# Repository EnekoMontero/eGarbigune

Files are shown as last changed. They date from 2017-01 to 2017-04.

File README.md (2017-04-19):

# eGarbigune :recycle:
 > Probably the cheapest mini 3D printer in the world. :moneybag:<br/>
 > Probablemente la mini impresora 3D más barata del mundo. :moneybag:

## Especificaciones principales
 - Mini impresora 3D hecha a partir de componentes reciclados
 - Replicable
 - Electrónica: Arduino Mega + Ramps 1.4
 - Firmware: Marlin
 - Volumen de impresión: 40x40x40 mm^3 teóricos
 - Sistema de ejes cartesianos
 - Hotend tipo J-Head con bowden
 - Base nivelable sin cama caliente
 - Materiales: PLA
 - Velocidad: 20-40mm/s

## Instrucciones de montaje
[Índice - Guía de montaje](http://haudahau.com/vadedos/?p=906)
 1. [Lista de materiales](http://haudahau.com/vadedos/?p=952)
 2. [Preparando los lectores de cd/dvd](http://haudahau.com/vadedos/?p=982)
 3. [Impresión de piezas](http://haudahau.com/vadedos/?p=1000)
 4. [Montaje de la estructura y del extrusor](http://haudahau.com/vadedos/?p=1026)
 5. [Electrónica y cableado](http://haudahau.com/vadedos/?p=1057)
 6. [Calibración y primera pieza](http://haudahau.com/vadedos/?p=1081)
 7. [Ponerla "coqueta", últimos detalles](http://haudahau.com/vadedos/?p=1115)
 8. Anexo
	 1. [Comprobar que los motores se mueven](http://haudahau.com/vadedos/?p=843)
	 2. [Añadir una impresora 3D en el Cura](http://haudahau.com/vadedos/?p=1095)
 9. Sácale fotos y házmelas llegar vía [twitter](https://twitter.com/enekomontero) u otros medios para añadirlas en GitHub :grin:

## Fotos
Fotos | :camera:
-------- | ---
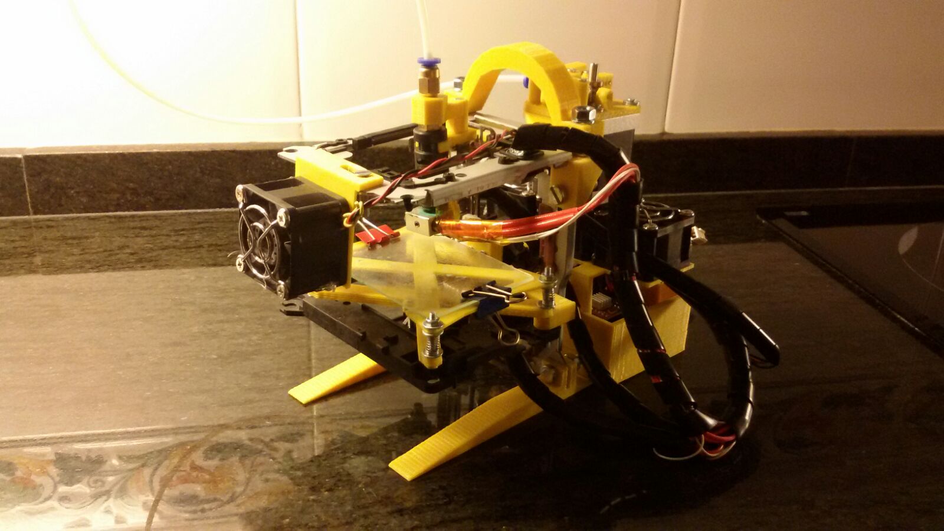
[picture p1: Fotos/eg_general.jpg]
general
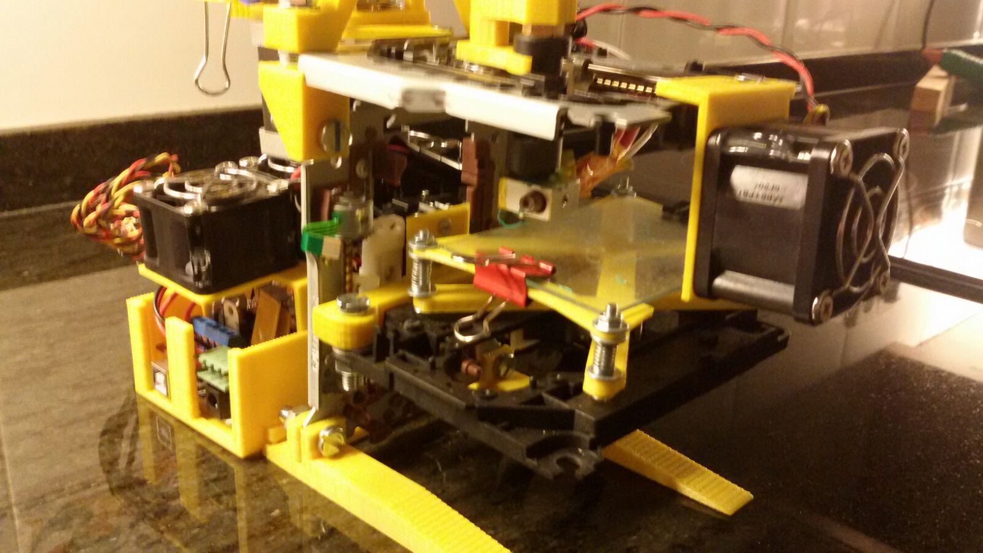
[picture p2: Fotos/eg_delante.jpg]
delante
  |  
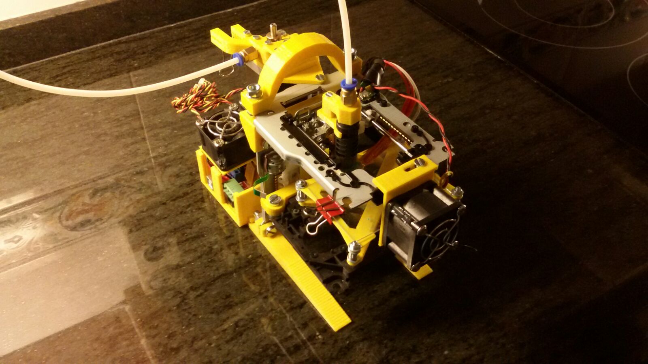
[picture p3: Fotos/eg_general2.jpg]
general2
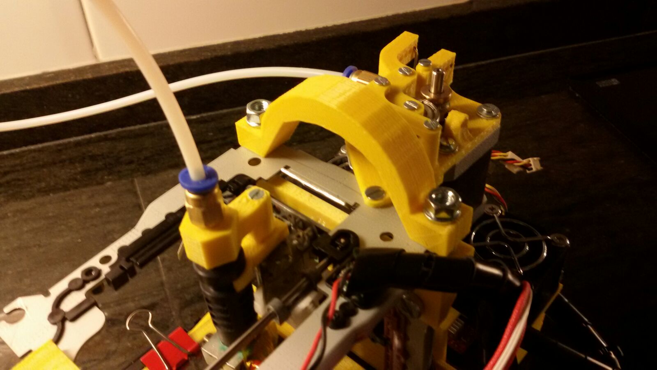
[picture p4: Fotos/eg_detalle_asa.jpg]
detalle asa
 |  
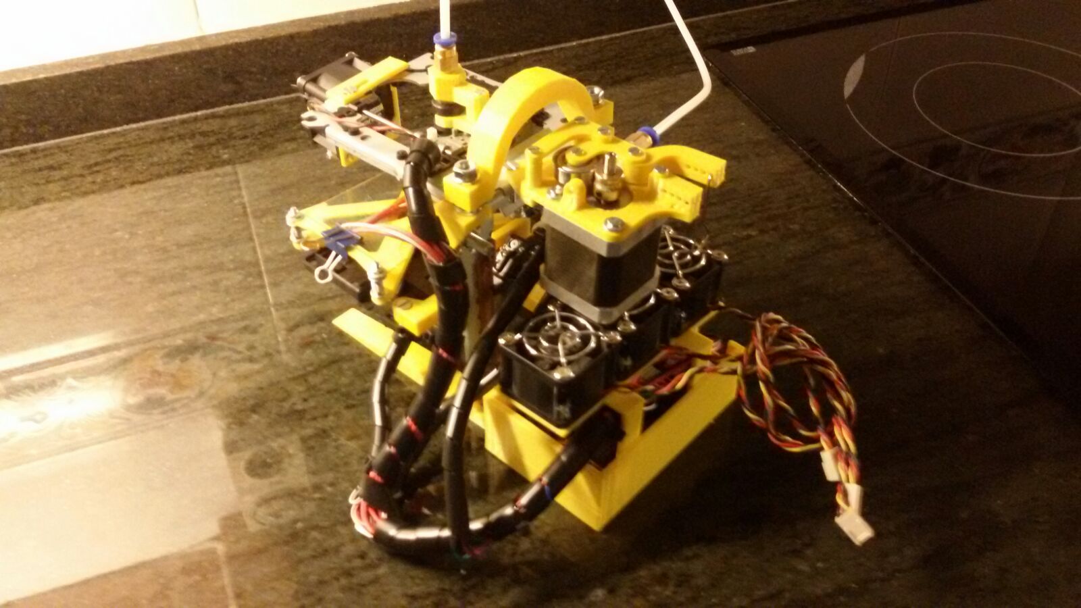
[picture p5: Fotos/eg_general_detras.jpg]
general detras
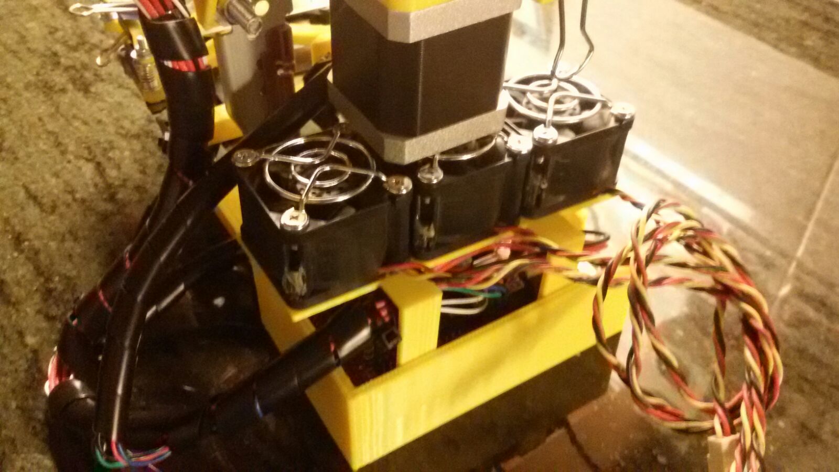
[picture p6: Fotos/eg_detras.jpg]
detrás
  |  
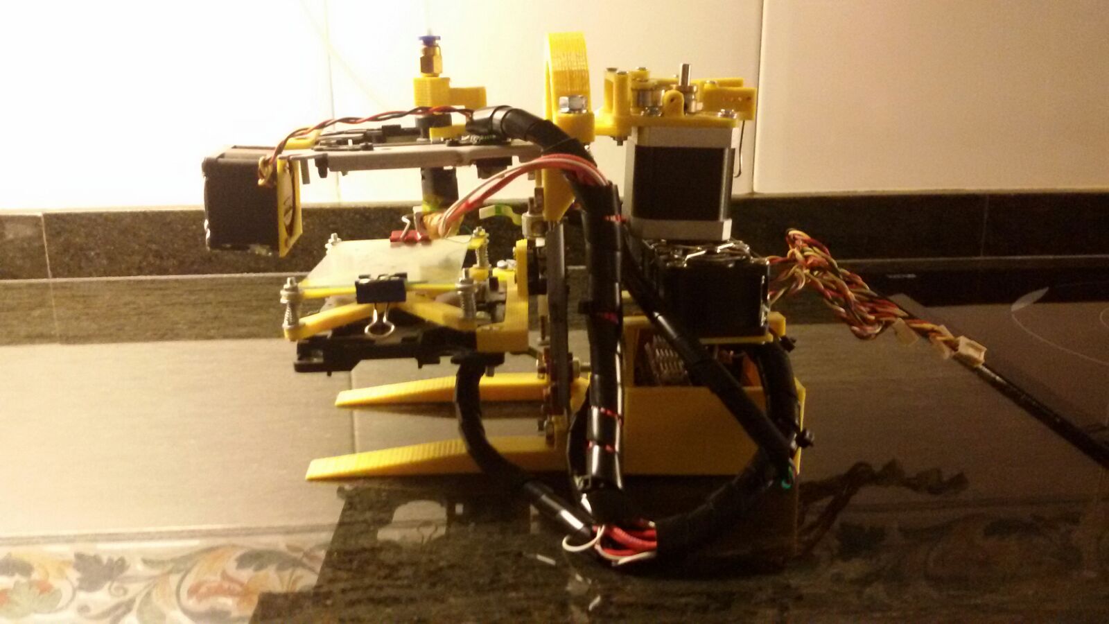
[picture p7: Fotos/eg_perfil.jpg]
perfil
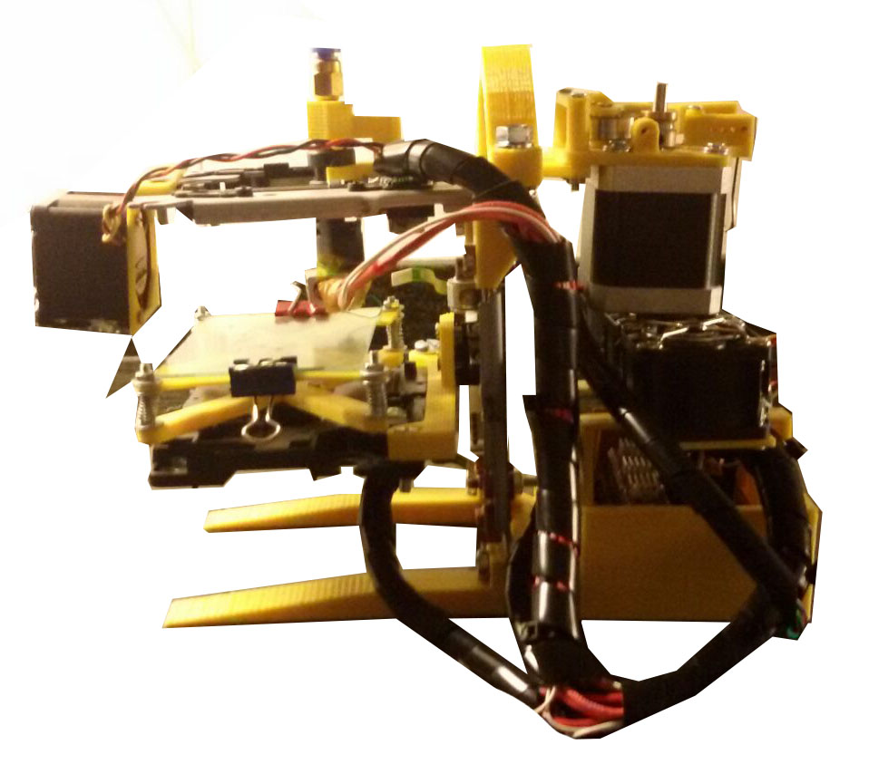
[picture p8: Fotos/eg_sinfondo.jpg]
perfil sin fondo
 |  

## eGarbigunes por el mundo :earth_africa:
Samuel Gil | :round_pushpin: Santiago de Compostela
-------- | ---
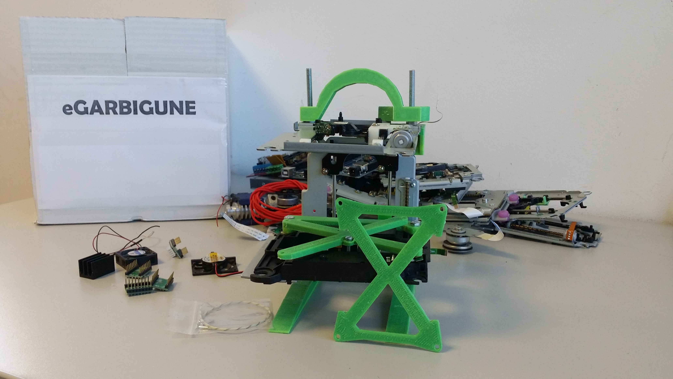
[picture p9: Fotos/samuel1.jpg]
samuel1
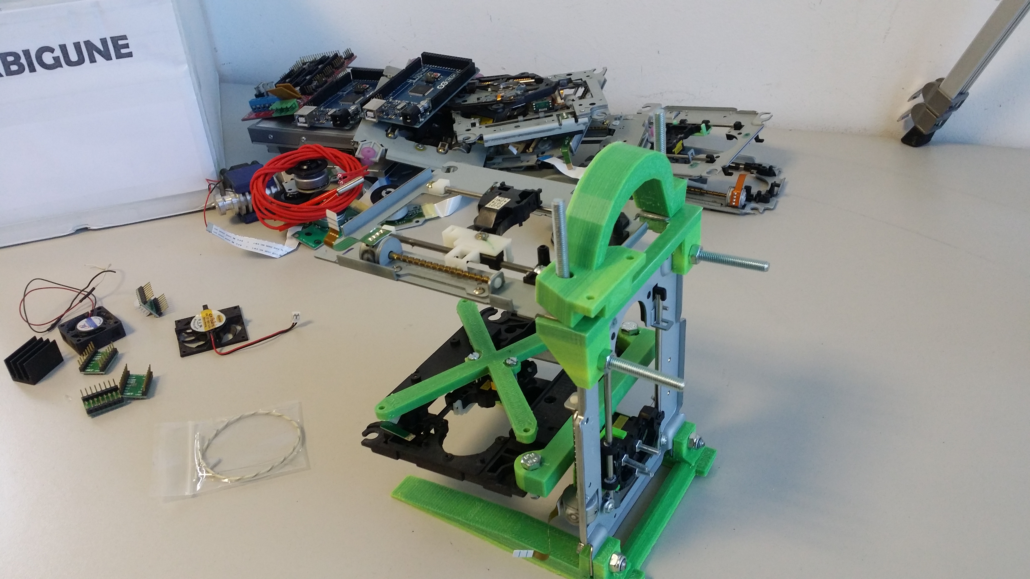
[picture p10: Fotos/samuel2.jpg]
samuel2
  | 

[bolsoncerrado](http://print3dforum.com/) | :round_pushpin: Barcelona
-------- | ---
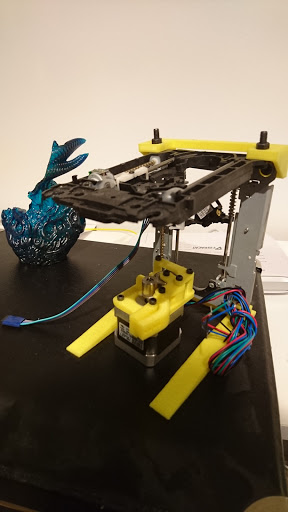
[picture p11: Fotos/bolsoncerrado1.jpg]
bolsoncerrado1
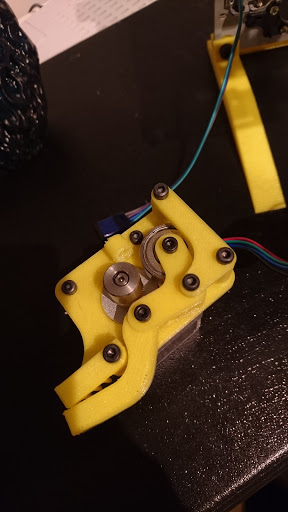
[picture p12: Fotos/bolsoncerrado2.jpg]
bolsoncerrado2
  | 
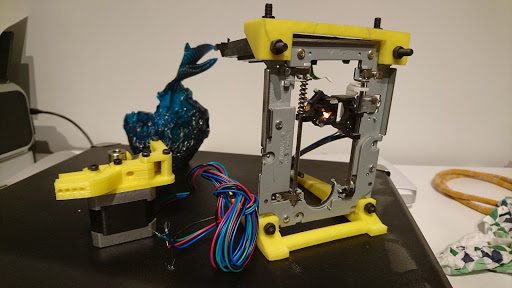
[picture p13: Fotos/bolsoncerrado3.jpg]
bolsoncerrado3
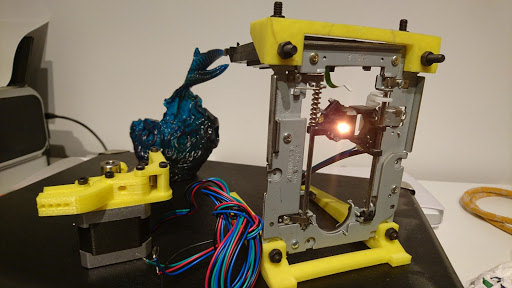
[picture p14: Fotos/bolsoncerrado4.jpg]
bolsoncerrado4
  | 

## Vídeos
 - Mini 3D Printer - First attempt [[youtube]](https://www.youtube.com/watch?v=VHxQsBB6kfk)
 - eGarbigune - Mini 3D Printer [[youtube]](https://www.youtube.com/watch?v=phJxERG1OLM&t=1s)
 
## Algunos artículos donde aparece
 - <http://haudahau.com/vadedos/?page_id=906>
 - <https://3dprint.com/94400/egarbigune-3d-printer/>
 - <http://impresiontresde.com/blog/egarbigune-una-mini-impresora-3d-reciclando-viejos-componentes-electronicos/>
 - <http://3dprintingfromscratch.com/2015/10/eneko-monteros-3d-printer-from-recycled-parts/>
 - <http://www.semageek.com/egarbigune-la-mini-imprimante-3d-fabriquee-avec-des-pieces-recyclees/>
 - <http://maker8.com/article-4497-1.html>
 - <http://www.3dhoo.com/news/guowai/21030.html>
 - <http://dimglobal.ning.com/group/roboticadonostia16/forum/topics/egarbigune-mini-impresora-3d-reciclada>

## Autor
 - Eneko Montero
 
## Licencia
<p style="text-align: justify;"><br/>
<a href="http://haudahau.com/vadedos/?page_id=906" target="_blank">eGarbigune</a> por <a href="https://es.linkedin.com/in/enekomontero" target="_blank" rel="cc:attributionURL">Eneko Montero</a> se distribuye bajo una <a href="http://creativecommons.org/licenses/by-sa/4.0/" target="_blank" rel="license">Licencia Creative Commons Atribución-CompartirIgual 4.0 Internacional</a>.</p>

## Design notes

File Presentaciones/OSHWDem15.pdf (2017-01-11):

# eGarbigune

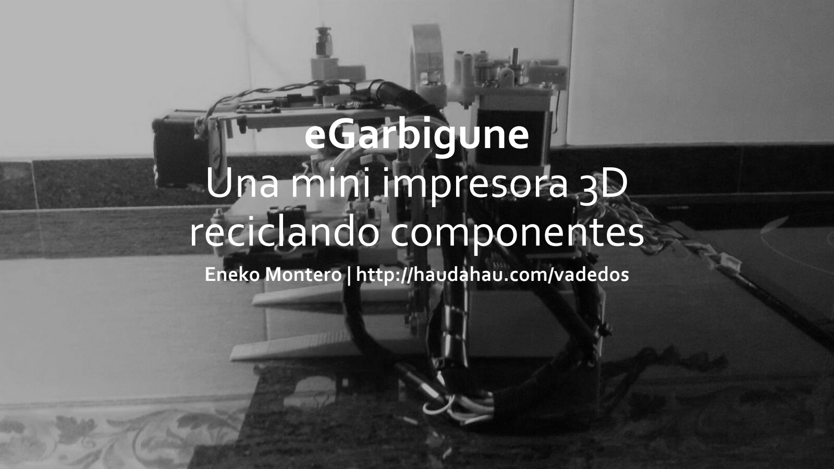
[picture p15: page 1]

# Una mini impresora 3D reciclando componentes

### Eneko Montero | http://haudahau.com/vadedos

# Especificaciones principales

- Mini impresora 3D hecha a partir de componentes reciclados
- Replicable
- Electrónica: Arduino Mega + Ramps 1.4
- Firmware: Marlin
- Volumen de impresión: 40x40x40 mm^3 teóricos
- Sistema de ejes cartesianos
- Hotend tipo J-Head con bowden
- Base nivelable sin cama caliente
- Materiales: PLA
- Velocidad: 20-40mm/s

# Proceso de montaje

### Lo que iba a ser y no fue

Se iba a basar en el proyecto eWaste,

### pero con una estructura impresa en 3D

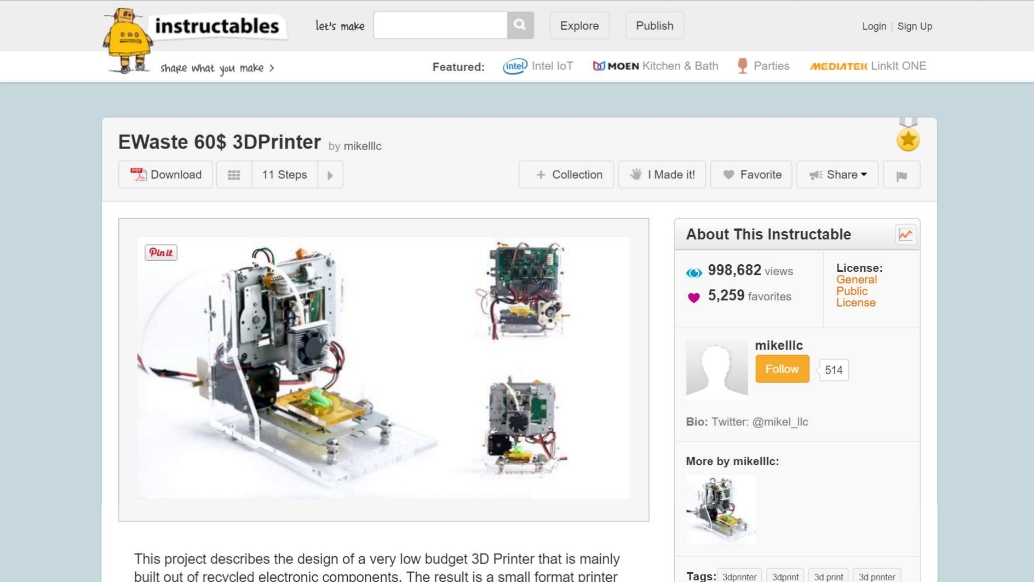
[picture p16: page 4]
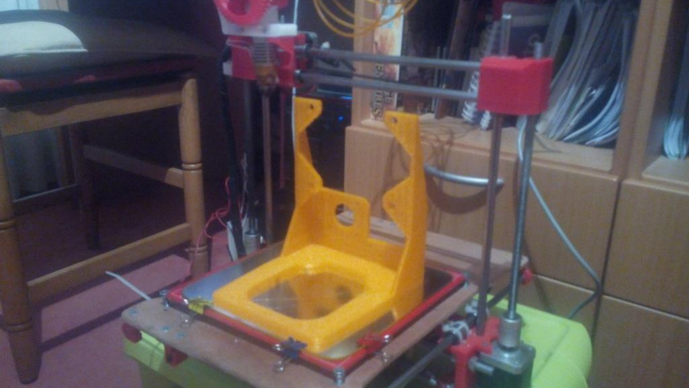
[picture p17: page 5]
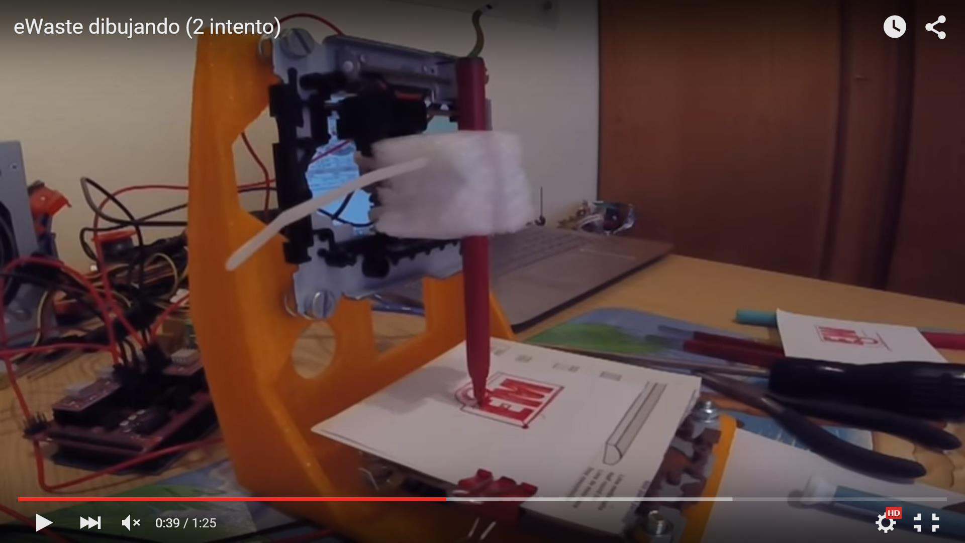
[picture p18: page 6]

# Encaminando el proyecto

Lo que finalmente fue, eGarbigune, misma idea, distinta ejecución

1. Reciclar lectores de cd/dvd
2. Imprimir las piezas necesarias para la estructura en 3D
3. Sistema de ejes distinto a eWaste

# Sistema de movimiento

Ejes cartesianos

- Eje X | Movimiento de la base de impresión con un lector de plástico.
- Eje Y | Movimiento del hotend con un lector metálico en la parte superior.
- Eje Z | Movimiento de la base con un único lector metálico en vertical. El lector del eje x va encajado a este. Comienza en la parte superior y va bajando según avanza la impresión.
- Homing | No lleva endstops, indicamos la posición (0,0,0) antes de comenzar la impresión.

## Reciclaje de lectores de

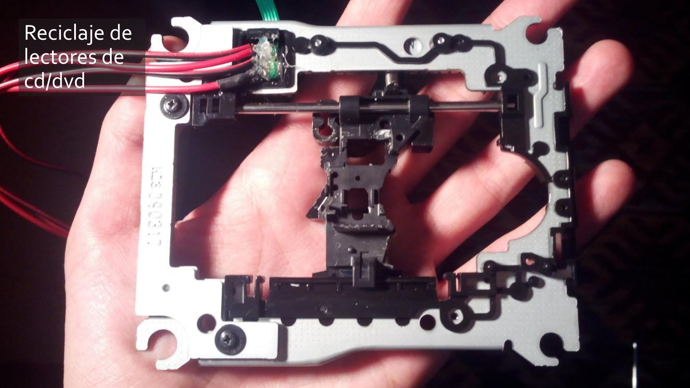
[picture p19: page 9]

## cd/dvd

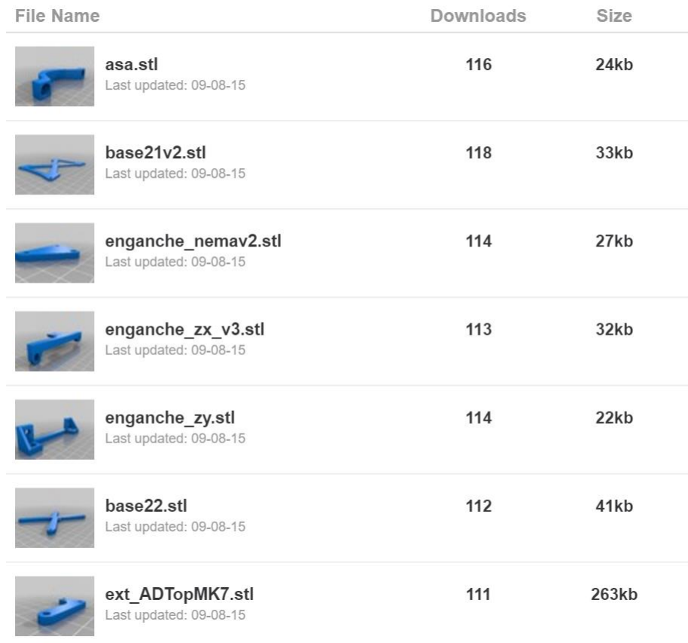
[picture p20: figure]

# Impresión de piezas

- Diseñadas usando SketchUp
- Se imprimen sin soportes*
- Se pueden descargar en Thingiverse (http://www.thingiverse.com/thing:1003982/#files)

*excepto una que no es necesaria en todos los casos

# Extrusor con bowden

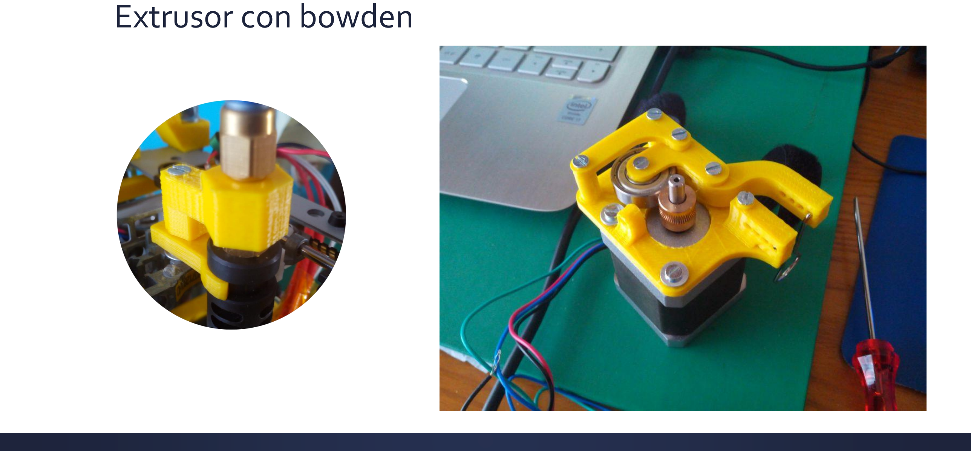
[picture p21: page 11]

# Primera pieza

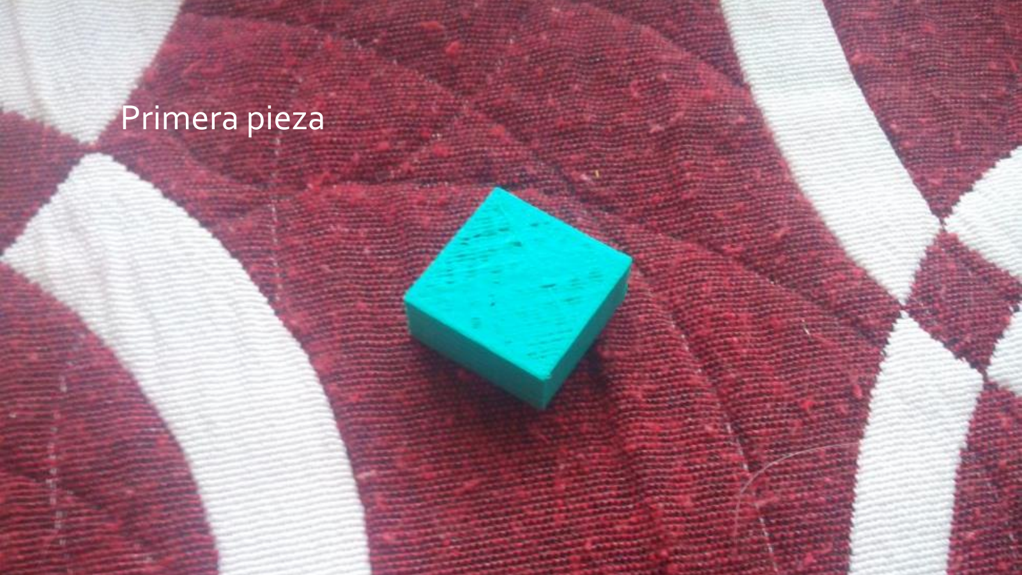
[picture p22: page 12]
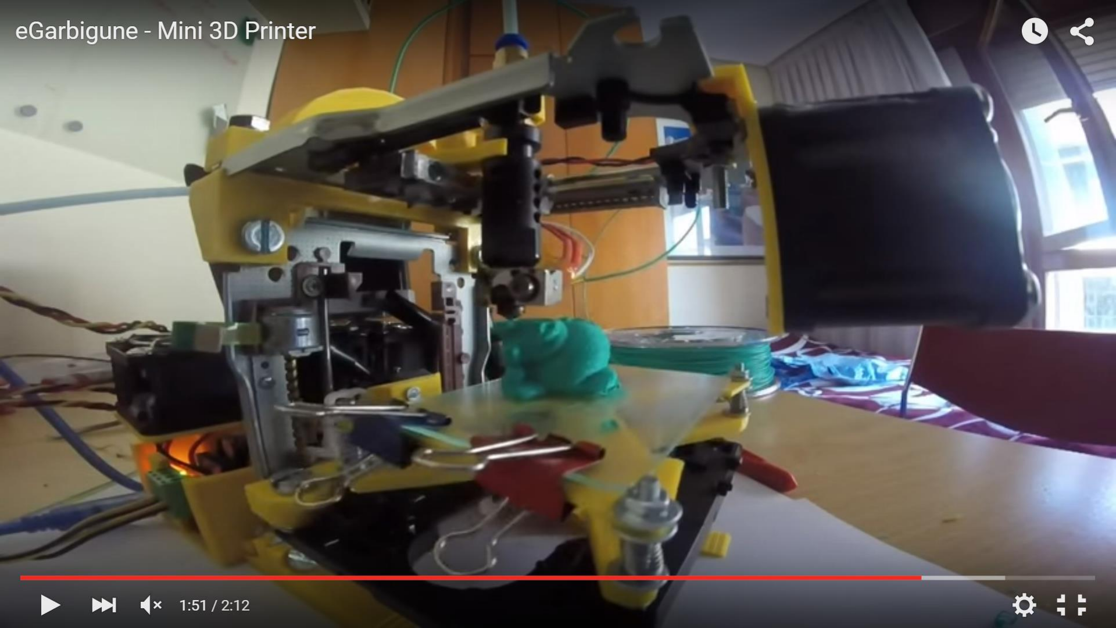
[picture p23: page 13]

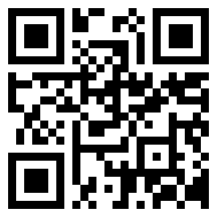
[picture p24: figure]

# FIN

### Eneko Montero

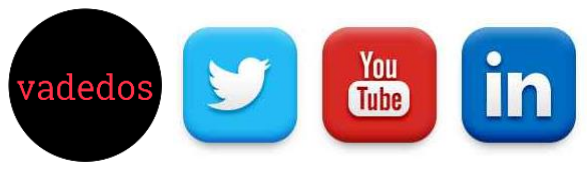
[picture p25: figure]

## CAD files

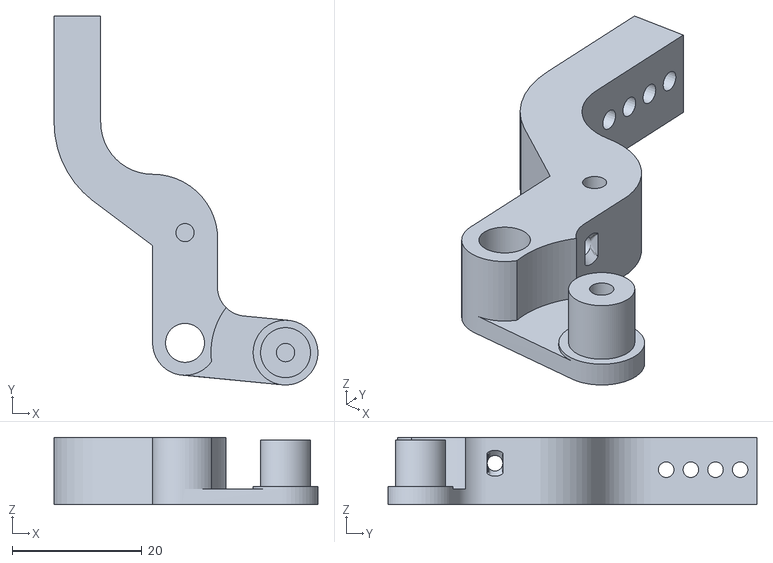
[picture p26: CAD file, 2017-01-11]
STL/ext_ADLowerArmMK7_R2.stl
40.7 x 56.9 x 10.4

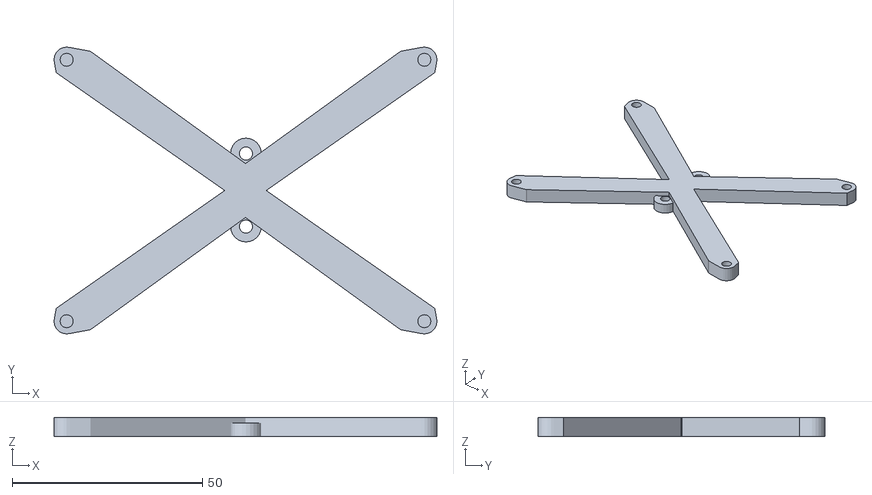
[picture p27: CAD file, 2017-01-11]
STL/base22.stl
100.6 x 75.3 x 5.00

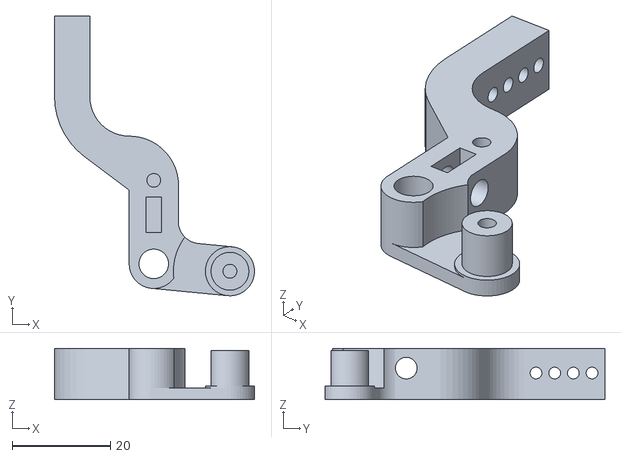
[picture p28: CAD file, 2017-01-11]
STL/ext_ADLowerArmAltMK7_R2.stl
40.7 x 56.9 x 10.4

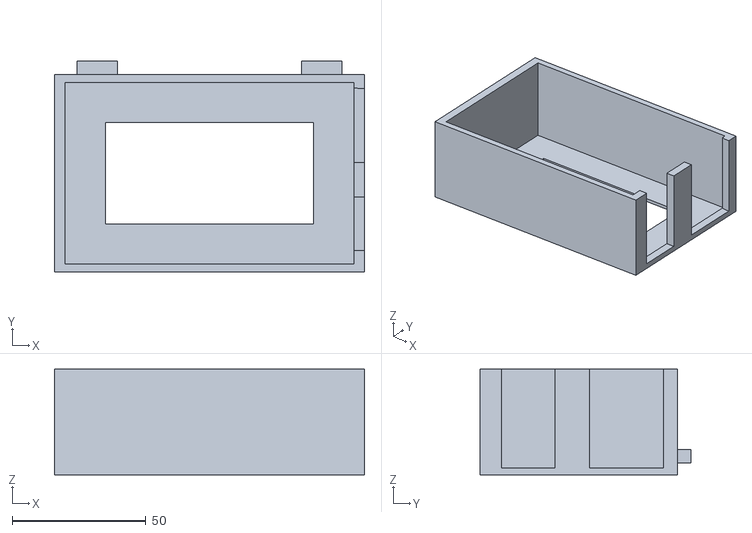
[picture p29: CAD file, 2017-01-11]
STL/rampscase.stl
116.0 x 79.0 x 39.5

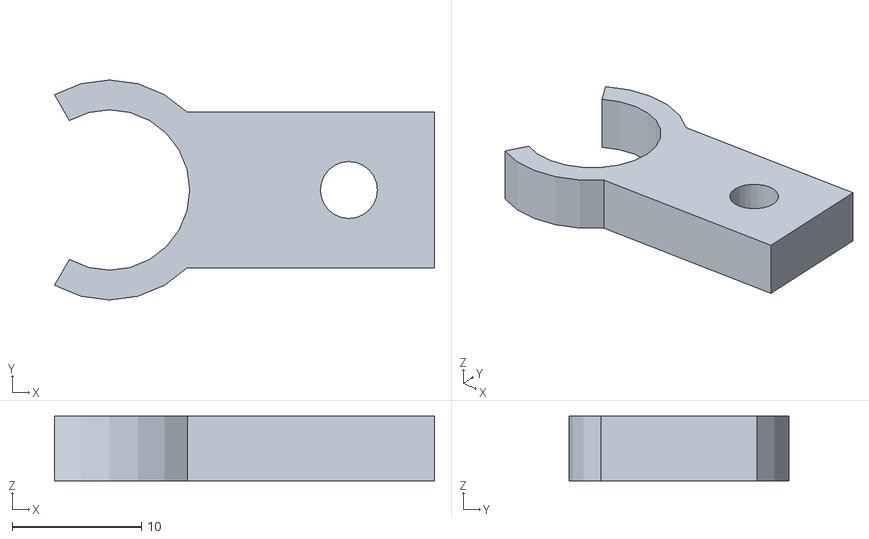
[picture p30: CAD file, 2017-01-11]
STL/soporte hotendv3.stl
29.4 x 17.0 x 5.00

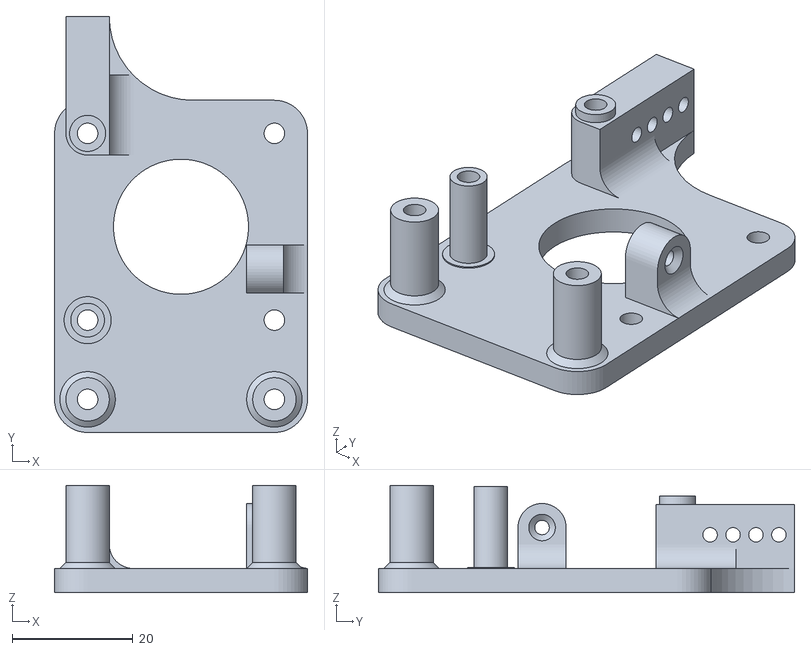
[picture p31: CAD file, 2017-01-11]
STL/ext_ADBaseMK7_R2.stl
42.0 x 69.0 x 17.8

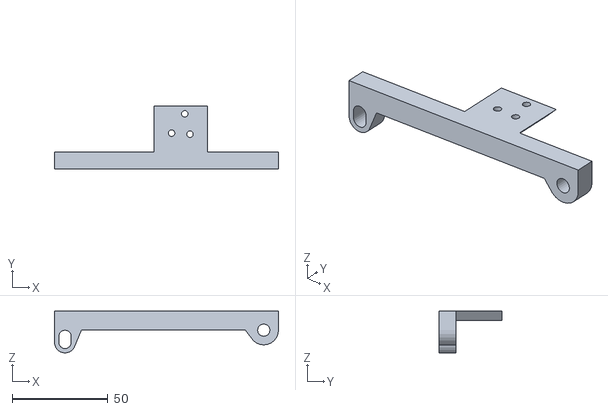
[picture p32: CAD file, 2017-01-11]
STL/enganche_zx_v3.stl
117.0 x 33.0 x 21.9

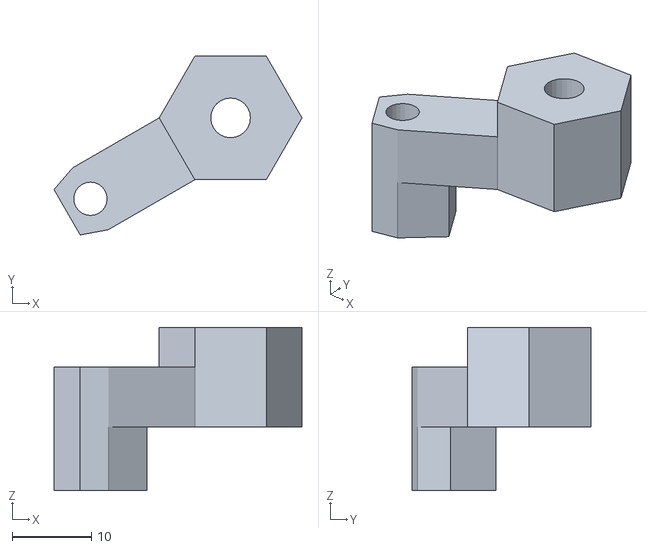
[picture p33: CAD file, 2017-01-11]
STL/racor.stl
31.3 x 22.5 x 20.6

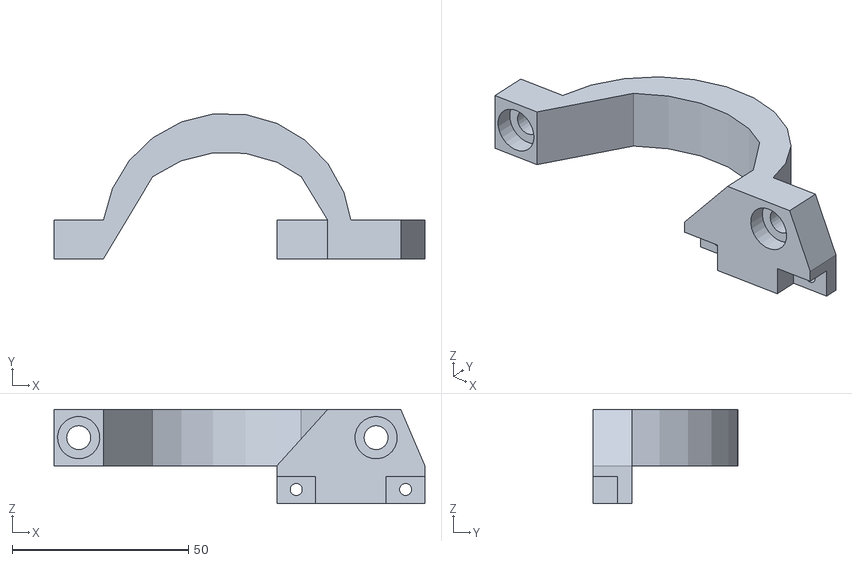
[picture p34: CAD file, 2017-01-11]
STL/asav2.stl
105.2 x 41.1 x 26.7

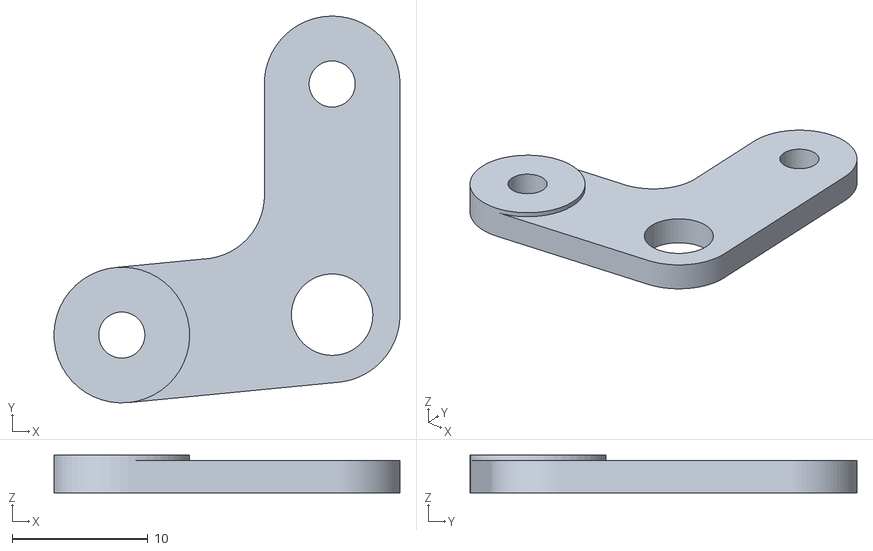
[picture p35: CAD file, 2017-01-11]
STL/ext_ADUpperArmMK7.stl
25.5 x 28.5 x 2.80

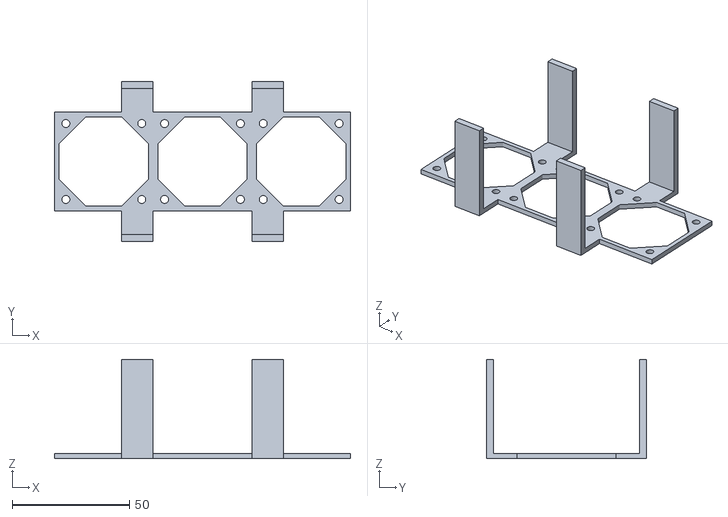
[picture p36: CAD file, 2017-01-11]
STL/vent_electro.stl
126.0 x 68.0 x 42.2

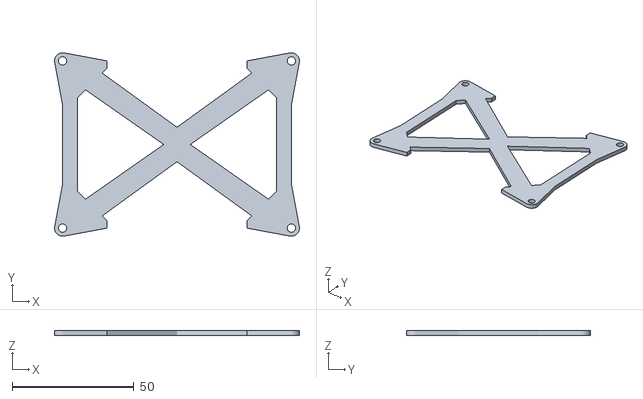
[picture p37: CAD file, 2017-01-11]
STL/base21v2.stl
100.6 x 75.3 x 2.00

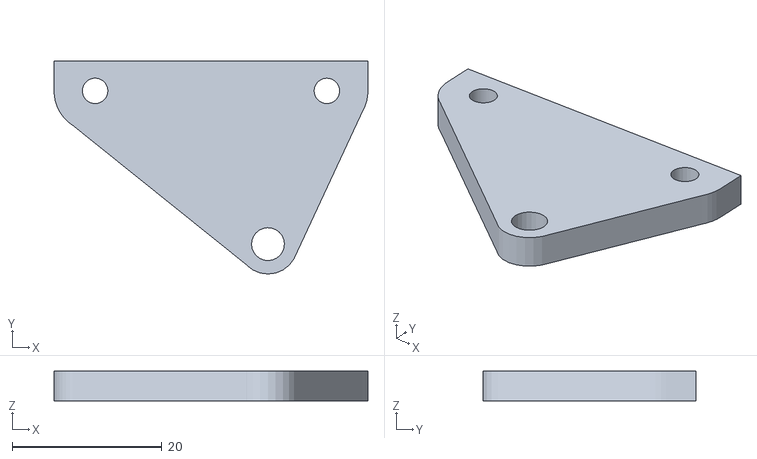
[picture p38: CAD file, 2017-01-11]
STL/enganche_nemav2.stl
42.0 x 28.5 x 4.00

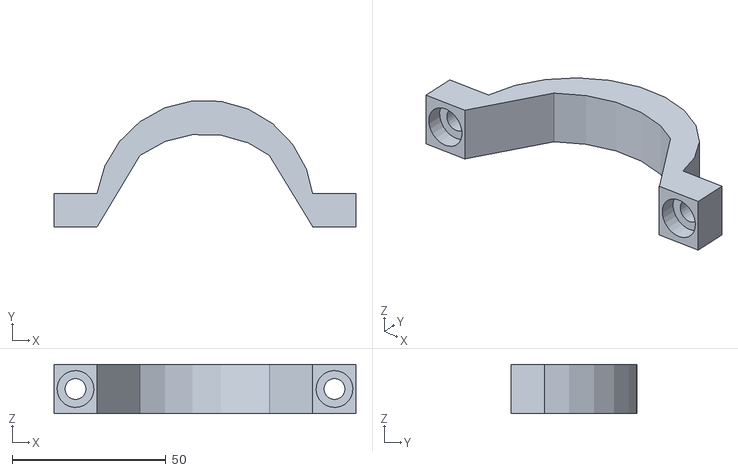
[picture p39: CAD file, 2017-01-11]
STL/asa.stl
98.3 x 41.1 x 16.0

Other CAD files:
STL/ext_ADTopMK7.stl
STL/vent_hotend.stl
STL/enganche_zy.stl
STL/patav2.stl
SKP/asa.skp
SKP/asav2.skp
SKP/base21v2.skp
SKP/enganche zx v3.skp
SKP/enganche zy.skp
SKP/enganche_nemav2.skp
SKP/patav2.skp
SKP/racor.skp
SKP/rampscase.skp
SKP/soporte hotend.skp
SKP/ventiladores.skp

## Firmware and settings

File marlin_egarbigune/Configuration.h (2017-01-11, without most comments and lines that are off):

#define CONFIGURATION_H
#define STRING_VERSION_CONFIG_H __DATE__ " " __TIME__ // build date and time
#define STRING_CONFIG_H_AUTHOR "Eneko Montero" //Who made the changes.
#define SERIAL_PORT 0
#define BAUDRATE 250000
#define MOTHERBOARD 33
#define POWER_SUPPLY 1
#define TEMP_SENSOR_0 5
#define TEMP_SENSOR_1 5
#define TEMP_SENSOR_2 5
#define TEMP_SENSOR_BED 5
#define TEMP_RESIDENCY_TIME 10	// (seconds)
#define TEMP_HYSTERESIS 3       // (degC) range of +/- temperatures considered "close" to the target one
#define TEMP_WINDOW     1       // (degC) Window around target to start the recidency timer x degC early.
#define HEATER_0_MINTEMP 0
#define HEATER_1_MINTEMP 0
#define HEATER_2_MINTEMP 0
#define BED_MINTEMP 0
#define HEATER_0_MAXTEMP 250
#define HEATER_1_MAXTEMP 250
#define HEATER_2_MAXTEMP 250
#define BED_MAXTEMP 130
#define PIDTEMP
#define PID_MAX 256 // limits current to nozzle; 256=full current
  #define PID_FUNCTIONAL_RANGE 10 // If the temperature difference between the target temperature and the actual temperature
  #define PID_INTEGRAL_DRIVE_MAX 255  //limit for the integral term
  #define K1 0.95 //smoothing factor withing the PID
  #define PID_dT ((16.0 * 8.0)/(F_CPU / 64.0 / 256.0)) //sampling period of the temperature routine
      #define  DEFAULT_Kp 26.31//19.22
      #define  DEFAULT_Ki 1.49//1.87
      #define  DEFAULT_Kd 115.97//49.45
#define MAX_BED_POWER 256 // limits duty cycle to bed; 256=full current
#define PREVENT_DANGEROUS_EXTRUDE
#define PREVENT_LENGTHY_EXTRUDE
#define EXTRUDE_MINTEMP 0
#define EXTRUDE_MAXLENGTH (X_MAX_LENGTH+Y_MAX_LENGTH) //prevent extrusion of very large distances.
  #define ENDSTOPPULLUP_XMAX
  #define ENDSTOPPULLUP_YMAX
  #define ENDSTOPPULLUP_ZMAX
  #define ENDSTOPPULLUP_XMIN
  #define ENDSTOPPULLUP_YMIN
  #define ENDSTOPPULLUP_ZMIN
const bool X_ENDSTOPS_INVERTING = true; // set to true to invert the logic of the endstops.
const bool Y_ENDSTOPS_INVERTING = true; // set to true to invert the logic of the endstops.
const bool Z_ENDSTOPS_INVERTING = true; // set to true to invert the logic of the endstops.
#define X_ENABLE_ON 0
#define Y_ENABLE_ON 0
#define Z_ENABLE_ON 0
#define E_ENABLE_ON 0 // For all extruders
#define DISABLE_X false
#define DISABLE_Y false
#define DISABLE_Z true
#define DISABLE_E false // For all extruders
#define INVERT_X_DIR false    // for Mendel set to false, for Orca set to true
#define INVERT_Y_DIR true    // for Mendel set to true, for Orca set to false
#define INVERT_Z_DIR false     // for Mendel set to false, for Orca set to true
#define INVERT_E0_DIR false   // for direct drive extruder v9 set to true, for geared extruder set to false
#define INVERT_E1_DIR false    // for direct drive extruder v9 set to true, for geared extruder set to false
#define INVERT_E2_DIR false   // for direct drive extruder v9 set to true, for geared extruder set to false
#define X_HOME_DIR -1
#define Y_HOME_DIR -1
#define Z_HOME_DIR -1
#define min_software_endstops false //If true, axis won't move to coordinates less than HOME_POS.
#define max_software_endstops true  //If true, axis won't move to coordinates greater than the defined lengths below.
#define X_MAX_POS 40
#define X_MIN_POS 0
#define Y_MAX_POS 40
#define Y_MIN_POS 0
#define Z_MAX_POS 40
#define Z_MIN_POS 0
#define X_MAX_LENGTH (X_MAX_POS - X_MIN_POS)
#define Y_MAX_LENGTH (Y_MAX_POS - Y_MIN_POS)
#define Z_MAX_LENGTH (Z_MAX_POS - Z_MIN_POS)
#define MANUAL_X_HOME_POS 0
#define MANUAL_Y_HOME_POS 0
#define MANUAL_Z_HOME_POS 0
#define NUM_AXIS 4 // The axis order in all axis related arrays is X, Y, Z, E
#define HOMING_FEEDRATE {50*60, 50*60, 4*60, 0}  // set the homing speeds (mm/min)
#define DEFAULT_AXIS_STEPS_PER_UNIT   {4.38747384,6.52920863,6.41933036,327.361519}  // default steps per unit for ultimaker
#define DEFAULT_MAX_FEEDRATE          {200, 200, 200, 50}    // (mm/sec)
#define DEFAULT_MAX_ACCELERATION      {600,600,600,3000}    // X, Y, Z, E maximum start speed for accelerated moves. E default values are good for skeinforge 40+, for older versions raise them a lot.
#define DEFAULT_ACCELERATION          400    // X, Y, Z and E max acceleration in mm/s^2 for printing moves
#define DEFAULT_RETRACT_ACCELERATION  2000   // X, Y, Z and E max acceleration in mm/s^2 for r retracts
#define DEFAULT_XYJERK                5.0    // (mm/sec)
#define DEFAULT_ZJERK                 0.4     // (mm/sec)
#define DEFAULT_EJERK                 5.0    // (mm/sec)
#define ULTIPANEL  //the ultipanel as on thingiverse
#define PLA_PREHEAT_HOTEND_TEMP 180
#define PLA_PREHEAT_HPB_TEMP 70
#define PLA_PREHEAT_FAN_SPEED 255		// Insert Value between 0 and 255
#define ABS_PREHEAT_HOTEND_TEMP 240
#define ABS_PREHEAT_HPB_TEMP 100
#define ABS_PREHEAT_FAN_SPEED 255		// Insert Value between 0 and 255
  #define NEWPANEL  //enable this if you have a click-encoder panel
  #define SDSUPPORT
  #define ULTRA_LCD
  #define LCD_WIDTH 20
  #define LCD_HEIGHT 4
#include "Configuration_adv.h"
#include "thermistortables.h"

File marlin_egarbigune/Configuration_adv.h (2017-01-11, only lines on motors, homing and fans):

#define ENDSTOPS_ONLY_FOR_HOMING // If defined the endstops will only be used for homing
#define X_HOME_RETRACT_MM 5
#define Y_HOME_RETRACT_MM 5
#define Z_HOME_RETRACT_MM 1
#define MICROSTEP1 LOW,LOW
#define MICROSTEP2 HIGH,LOW
#define MICROSTEP4 LOW,HIGH
#define MICROSTEP8 HIGH,HIGH
#define MICROSTEP16 HIGH,HIGH
#define MICROSTEP_MODES {16,16,16,16,16} // [1,2,4,8,16]
#define DIGIPOT_MOTOR_CURRENT {135,135,135,135,135} // Values 0-255 (RAMBO 135 = ~0.75A, 185 = ~1A)

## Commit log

2017-01-11 Añadidos ficheros stl para imprimir
    [asa.stl, asav2.stl, base21v2.stl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]
2017-01-11 Añadidos ficheros sketchup para poder editar
    [asa.skp, asav2.skp, base21v2.skp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]
2017-01-11 Añadido firmware actual
    [Configuration.h, Configuration_adv.h]
2017-01-11 actualizada la info :grin:
2017-01-21 :camera: ¡Añadidas nuevas fotos!
